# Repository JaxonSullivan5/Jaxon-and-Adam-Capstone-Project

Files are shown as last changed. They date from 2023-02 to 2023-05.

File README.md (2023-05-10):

# Robotic Arm Capstone Project
(Written By: Adam Kirkpatrick and Jaxon Sullivan)

5/10/23

IMG_9353 (1)

(Figure 1: Picture of Finished Arm)

**Design Summary:**

Our arm design is based off of the EEZYbotARM mk1 made by Carlo Franciscone. We like this design except for the fact that it only incorporates micro servos as opposed to using full sized servos. So we decided to make the design work for full sized servos that were to be used in the base and we figured we'd make the arm longer to maximize the filament limit. In the end, the arm basically functions by having a servo rotate the whole arm, a servo elevate the arm, and a separate servo extend the arm. In terms of controls we simply used the two thumb sticks for moving the arm and using the claw. (One stick controlls rotation/elevation, and the other stick controls extension/grabbing via the button inside the stick. In addition to the manual mode, we have an autonomous mode were we use a color sensor to give information to the servos (so they can sort objects based on thier color) and a rgb LED to display the color of the object detected. Finally, we used a switch to change between the two different modes.

Screenshot 2023-05-10 7 01 51 AM

(Figure 2: Original EEZYbotARM mk1 made by Carlo Franciscone.)

**System Details:**

This system uses three servos, one for rotation, one for elevation, and one for exntension of the arm. The servo used for rotation is held within the lower base component while the servos used for elevation and extension are housed in the upper base where one is directly connected to the main arm piece while the other one is connected to an extended servo horn piece that in and of itself is connected to the main upper arm section. On the tip of the arm connecting the main and secondary upper sections is the claw section. In this section there is a micro servo that is placed upside down and it is connected to a set of gears that have extensions on them to make the actual pincer of the claw. It is important to note that the color sensor is taped on the front of the micro servo so it can get the most accurate color reading from the object that is being picked up. The rgb LED and the switch that is used for switching between the autonomous and manual modes are both situated on a breadboard that is the hub for almost all of our wiring.


(Figure 3: Picture of extended servo horn, main lower beam, main upper beam, and triangular beam in order from farthest to closest.)

**Design Evaluation:**

* This project meets the Output Display requirement via using an rgb LED that returns readings from the color sensor.
* The Manual User input requirement is met by having a manual control mode with two thumb sticks where the used has full controll over the system. User Input is also seen with the switch that allows for the user to switch to the autonomous mode if they so please.
* This project meets the Automatic Sensor requirement because of the aforementioned color sensor that directs the arm to sort objects in predestined locations based on their color.
* The Actuators, Mechanisms, and Hardware requirement is fufilled thanks to the numerous servos, the gears in the claw, and the system of linkages that connects the whole system.
* Our project also meets the Logic, Processing, and Control via having programmed logic with the color sensor based autonomous mode and the calculations achieved to use the sticks in the manual mode.

s0ic0gcptmxqpj12s85jhcdotcco
(Figure 4: Close-Up picture of a Deego-FPV servo)

**Parts List:**

* Three Deegoo-FPV Servos costing $15 dollars in total
 (Model Number MG995)
* One HiTec mircro servo costing $2.50
 (Model Number SG90)
* One HiLetgo color sensor costing $7
 (Model Number TCS34725)
* One ELEGOO MEGA R3 Board ATmega 2560 costing $21
 (Model Number LYSB01H4ZDYCE-ELECTRNCS)
* One HiLetgo bread board costing $2.50
 (Model Number 3-01-0192)
* WGCD thumbsticks costing $4.80
 (Model Number 8542140575)
* EDGELEC rgb LED costing $0.09
 (Model Number ED_YW05_RGB-4P-C)
 TOTAL COST: $52.89

(Note: You will obviously also need all of the 3d printed parts which you can print via the stl files in this repository.)

 **Lessons Learned**
 
 During this project we learned mostly about how to code the color sensor and the thumb sticks. This process involved copying sample code for these components, modifying said code, and then integrating it into the system. This was difficult when we had to merge our autonomous and manual modes. Secondly, we learned how to use many different tools in onShape to design our parts to be as structurally strong and clean in appearance. Specifically, we heavily used drafts, fillets, and extrudes to make our model have a smooth appearance. We learned how to use the draft for the triangle like piece on the top of the main arm and the extrusion off the upper base. These parts also required partial fillets until we combined their seperate sections by using the boolean function. We used fillets everywhere except for the bottom of the base pieces because we wanted those pieces to sit flat against whatever surface we mounted them on. We extruded all of our parts from the bottom up and removed sections by using horizontal removal extrudes. We were going to make a custom claw piece in addition to the rest of our parts; however, we didn't get the chance to do so because of time constraints. Instead, we just used the orginal claw piece because is suites our purposes well enough. My recomendation to any future robotics student is to not overcomplicate your 3d modeled designs unless you have the time to make them look and function perfectly.
 
Screenshot 2023-05-10 7 48 10 AM

(Figure 5: Screenshot highlighting the use of drafts and fillets on the triangular beam in particular)

 **Instructions for assembly**

1. You will need all of the parts listed above in the parts list along with some wires, 220 resistors, a 0.5 cm brass pipe that will be cut to be 3.5 centimeters long, 0.4 centimeter screws, and 0.4 centimeter nuts. All of your screws thould be roughly 1.5 centimeters long except for one screw which should be about 3.5 centimeters long. (Note that you will need a screw driver and/or a wrench of some sort to secure the parts in addition to some tape or hot glue.) 

2. Make sure you have all the 3d printed parts which include 3 small long beams, the main lower beam, the extended servo horn beam, the main upper beam, the triangular beam, and the claw pieces. 

3. Assemble your arm by following these simple steps:

* First, drop your servo into the bottom base piece and screw it in, make sure you feed the wire out of the holes provided so the the arm sits flat on the table.

* Next, attach whatever t shaped servo horn that came with your servo to the previously mentioned servo and then place the top base piece onto it. (There is a box that the servo horn should fit into.)

* Then secure the servo horn to the top base via tape or hot glue.
* Proceed to fit your other two servos into the sides of your top base and secure them with screws.

* Advance by fitting the servo horns into the servos and then putting them into the main lower beam and extended servo horn pieces respectively. (Note that the side with the extended servo horn should be opposite to the upper base with the frontal extrustion.

* Continue via sliding the brass pipe through the extended servo piece, the central extrusion, and the main beam. Make sure that it's as tightlu fitted as posible from one servo horn to anather.

* Then put the triangular beam in the smaller of the two top notches in the main beam, ensure that the elevated and shortest extrusion is facing away from the top base's extrusion.

* Begin to put the main upper beam into the bigger notch of the main lower beam. Make sure the middle hole of the main upper beam is the on lined up with the holes of the triangular piece and the main lower beam. Then you can fit your long 3.5 centimeter screw through all three of these parts. (Note: The longer side of the main upper beam should face the same direction as the shorter side of the triangular piece.

* Go ahead and connect the upper base's extrusion to the long side of the triangular piece via a small beam, then use another small beam to connect the end of the servo horn extrustion piece to the shorter side of the main upper beam.

* Proceed to connect your final small beam from the small side of the triangular piece to the upper part of the claw platform and connect tbe long end of the main upper beam to the lower part of the claw platform

* Finally, just assemble the claw section by inserting the micro servo, screwing in its shortened servo horn with its claw pinchers and gears. 

(Also, don't forget to tape in your color sensor onto the front of the mirco servo and wire up all your connections with your thumb sticks if you have them)

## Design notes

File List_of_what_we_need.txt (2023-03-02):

1) Five Mirco Servos
2) Two analog sticks
3) Arduino board
4) Arduino Prototype sheild
5) Camrea??
6)
7)

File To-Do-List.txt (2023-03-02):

Here is what needs to be done:
1) Model and print the linkages needed
2) Learn to use an analog stick to give feedback
3) Order the micro servos that are needed
4) Print the part that holds the Analog sticks

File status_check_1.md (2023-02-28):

Project Status Check 1 questions:

1. Which parts of the project have you begun constructing to get to the final working solution?

We have started an onShape project to begin designing the base plate that we will 3D print for our assembly to sit on top. The plate will
sit on top of a standard 125 tooth rev gear so it can effectively rotate. We have also started citing sources on a google doc.

2. Have you ordered all additional parts that will be needed?  When will they arrive if they have not already?

No, we have not ordered any parts yet as we are currently just solidifying the design.

3. Have you designed any of the parts that will need to be manufactured?  If not, when will those designs be done?

Yes, we have designed the base plate that our arm will sit on and we have started to design exterior plates for the arm to help make it look nice.

4. If you are able to complete the project by May 13th to your expectations, will you receive full credit in all five functional element categories?

Yes, we should be able to meet all five requirements by using LEDs to display outputinformation, a controller for human input,
a distance sensor/camera for sensors, a bunch of servos and motors for the mechanisms, and we will used programmed logic in conjunction with the
distance sensor/camera for Logic, Processing, and Control.

5. What are the three most significant design challenges you foresee for this project?

Weight distribution with the arm, scaling of the arm, and using a sensor with the arm. Weight distribution will be a problem because our arm will primarily need to be acurate rather than powerful. Yet, it should be able to lift something heavier than a paperclip. Scalling will be hard because we will need to make our arm a convenient size to carry, yet not have it be tiny and weak. Finally, learnign to code a sensor with the arm will be a significant challenge because we will have to use a lot of programmed logic to get it to work propperly.

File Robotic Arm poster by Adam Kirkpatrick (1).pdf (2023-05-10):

# CODING PROCESS

# ARM DESIGN PROCESS

# ASSEMBLY PROCESS

# PROJECT OVERVIEW

# Robotic Arm Project

# by Adam Kirkpatrick and Jaxon Sullivan

Our arm design took heavy inspiration from the EEZYbotARM mk1 made by Carlo Franciscone. We liked his design but we wanted our arm to be bigger and use the full size servos instead of micro servos. With those two goals in mind, we started to scale the arm up by a scale factor of two only to realize that the arm was not only too big considering our filament limit, but that it also was unnecessarily wide. In light of this, we changed our dimensions and printed our improved design. We quickly realized that there were several measurement errors that involved our bottom base not being centered with our top base, and our screw hole size not properly accounting for the 3d printer's slight lack of precision. On our next print we would make the hole sizes larger for the servo head mountings yet smaller in most places to fit rev screws. After the second round of design changes our prints came out and fit together properly.

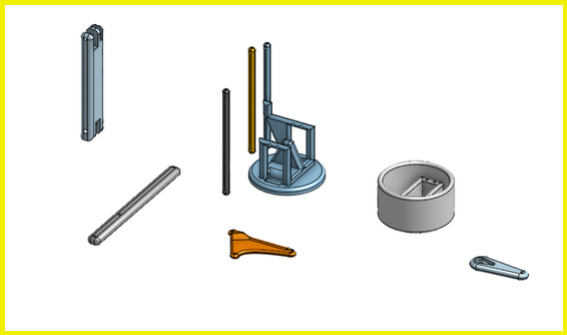
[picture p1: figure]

(Figure 1: Picture of whole onShape Assembly)

Our coding process was challenging in the way that it uses a color sensor and two sticks which were components of circuitry that we were unfamiliar with up until this point. Besides that minor hurdle, the rest of the code just involved servo positions that correlated to stick positions and color sensor outputs. After a short while, we had set of code for the color sensor autonomous mode where arm would move to a set position and then proceed to pick up and move an object based on its color and then it would proceed to return to its initial position where another object could be placed in front of it. We also had a separate set of code for our manual control mode where the arm can be maneuvered via two thumb sticks. Then all that we needed to do was add an LED and a switch to integrate the two pieces of code and meet all standards of physical elements.

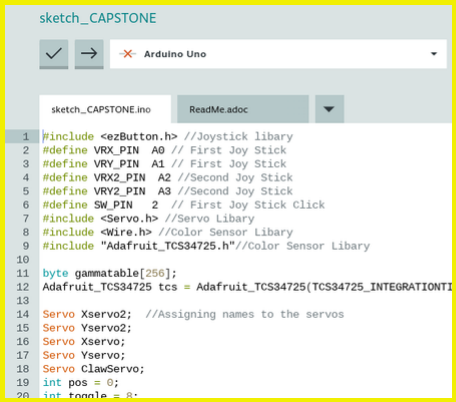
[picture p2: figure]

(Figure 2: Picture of code in Arduino IDE)

Our assembly Process was rather simple once we had all of the components. First we had to plug in our design via a breadboard and a copious amount of wires. This was rather repetitive considering that each of the two thumb sticks used six wires, each of the four servos (including one micro servo) used three wires, the color sensor used four wires, the LED used two, and the switch used three. We also opted to use a mini bread board to make all of this wiring compact. Then we had to construct the arm and do fine tuning to ensure that our arm was rotating to the correct positions. (This was important considering the fact that we used the previously mentioned kit arm from Carlo Franciscone to test our code before the arm was complete.) This was pretty straight forward because it just involved tweaking servo positions until the arm went exactly where we wanted it to. Finally, we just needed to wrap up the little things (such as this poster) and try to make our design as presentable as possible.

(Figure 3: Picture of Finalized Arm)

The Robotic Arm concept stemmed from the idea of creating an Iron Man type of arm that could be mounted on a person. We initially began development with this goal in mind until we realized that there was no way that we could make what we wanted within the 200 gram filament limit. So we quickly shifted gears to this more practical and flexible concept. We realized that we wanted an arm that could pick up small objects and sort them via user input, or a color sensor. We began to work on the design of the arm by basing it on another design that we conveniently had access to thanks to Mr. Cline. We also proceeded to learn how to use the color sensor with an rgb LED to meet the human input standard and properly display the color of what the sensor was seeing. We also promptly learned how to coordinate the sticks to move the arm around in an ergonomic manner. We always kept the one hundred dollar spending limit in mind via buying the cheapest servos, color sensor, and Arduino board possible. In the end we only used blank percentage of our budget. We also worked to test our manual and autonomous code before we even had our arm functioning by running it on the kit that we were basing our design off of. Finally, we created this poster, compiled our budget spread sheet, commented our code and integrated it all into our engineering notebook. We are pleased with the fruits of our labor because our design is not only practical, but it provided a great learning experience for how to properly design parts, code unique sensors, and format it all in a clean and organized way.

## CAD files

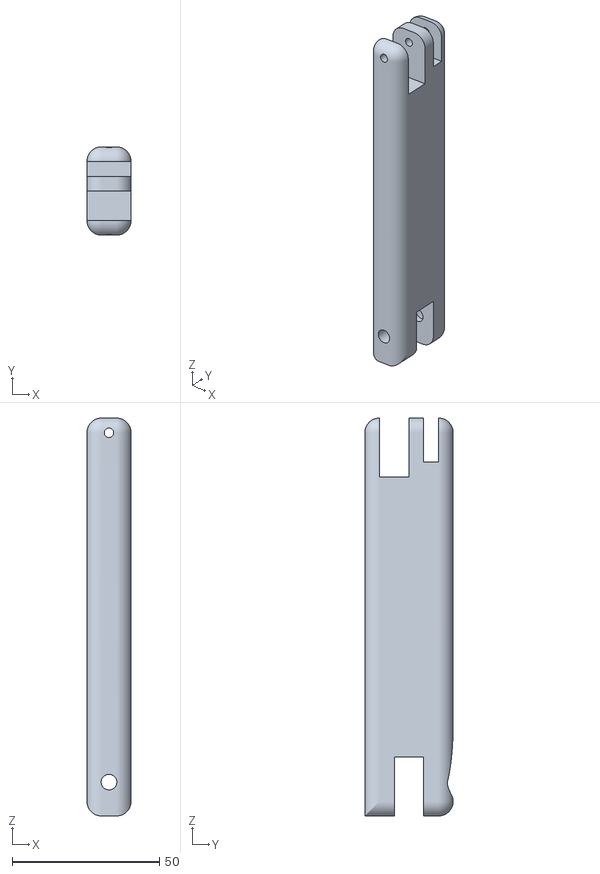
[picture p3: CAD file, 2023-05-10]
Main Lower Beam (Part 2).stl
15.0 x 30.0 x 135.0

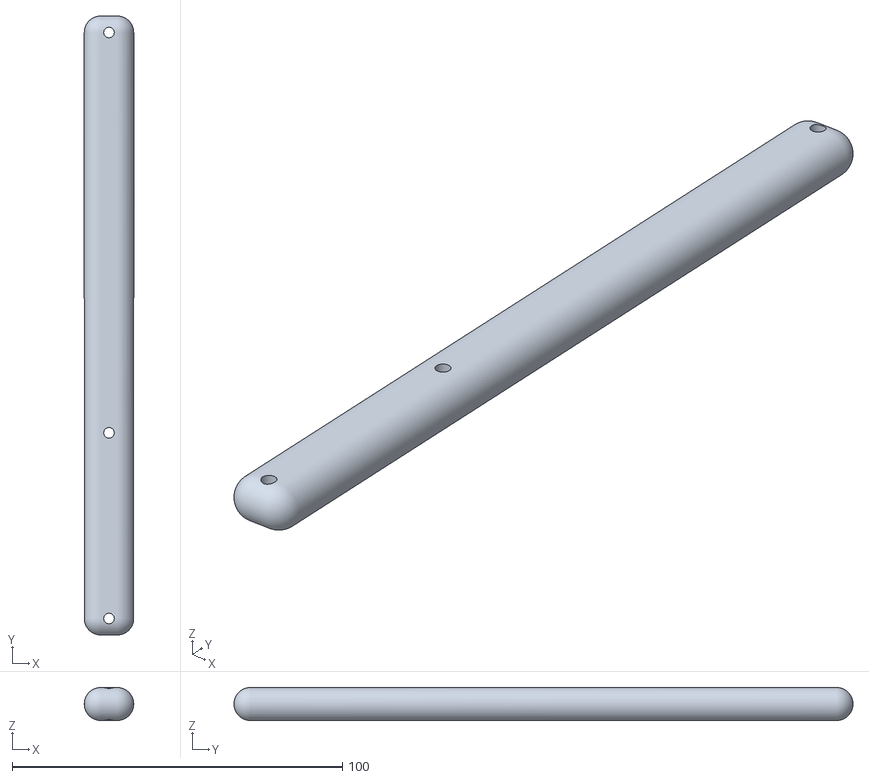
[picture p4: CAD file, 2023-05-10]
Main Upper Beam (Part 6).stl
15.0 x 187.5 x 10.0

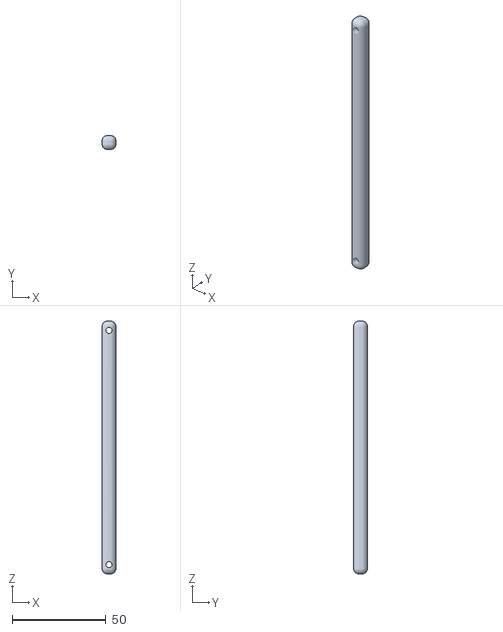
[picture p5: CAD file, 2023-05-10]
Small Beam (Parts 3, 4, and 5).stl
7.50 x 7.50 x 135.0

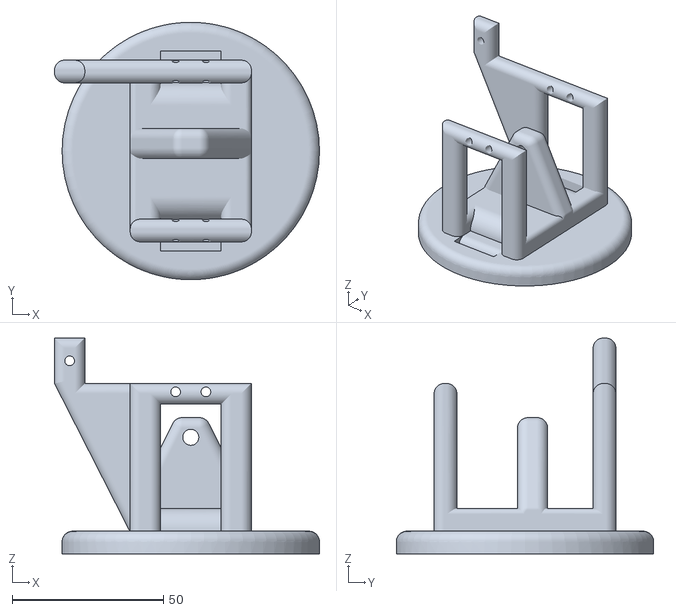
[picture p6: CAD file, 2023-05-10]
Upper Base (Part 1).stl
87.5 x 85.0 x 71.2

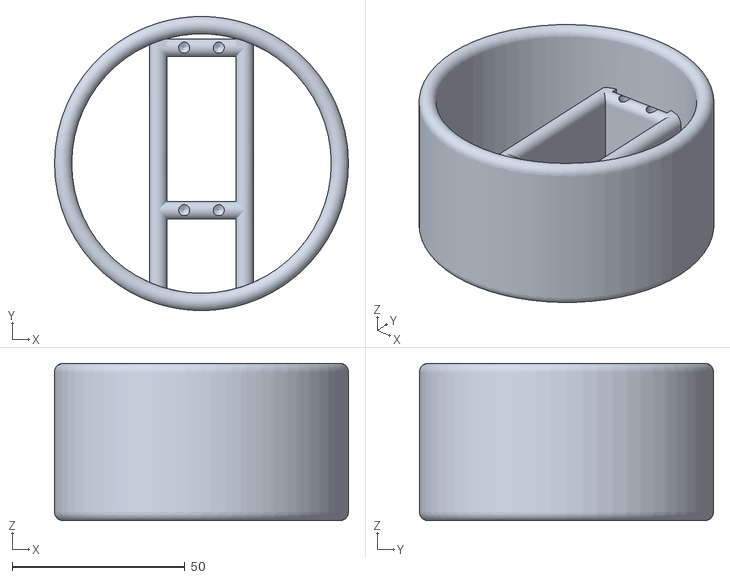
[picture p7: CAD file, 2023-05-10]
Lower Base (Part 7).stl
85.0 x 85.0 x 45.5

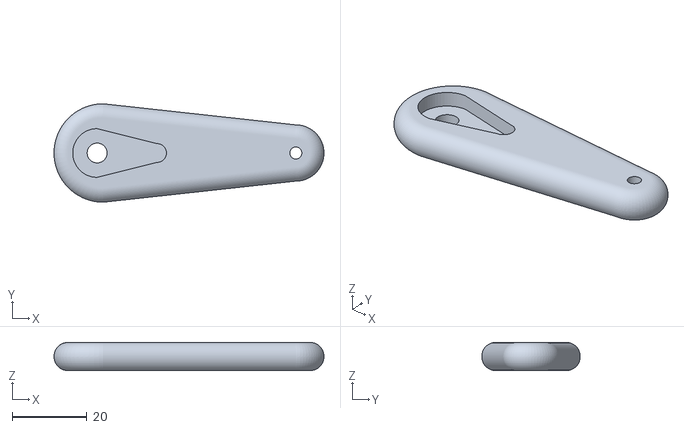
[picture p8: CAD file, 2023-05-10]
Extended Servo Horn (Part 8).stl
72.0 x 26.2 x 7.50

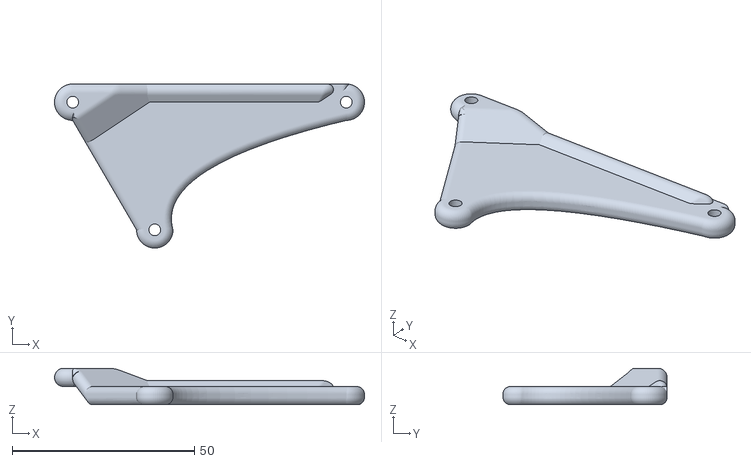
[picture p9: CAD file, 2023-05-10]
Triangular Beam (Part 9).stl
85.0 x 45.0 x 10.0
